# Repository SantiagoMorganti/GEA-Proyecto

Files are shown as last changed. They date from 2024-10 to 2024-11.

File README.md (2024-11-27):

<div align="center">

# PROYECTO GEA

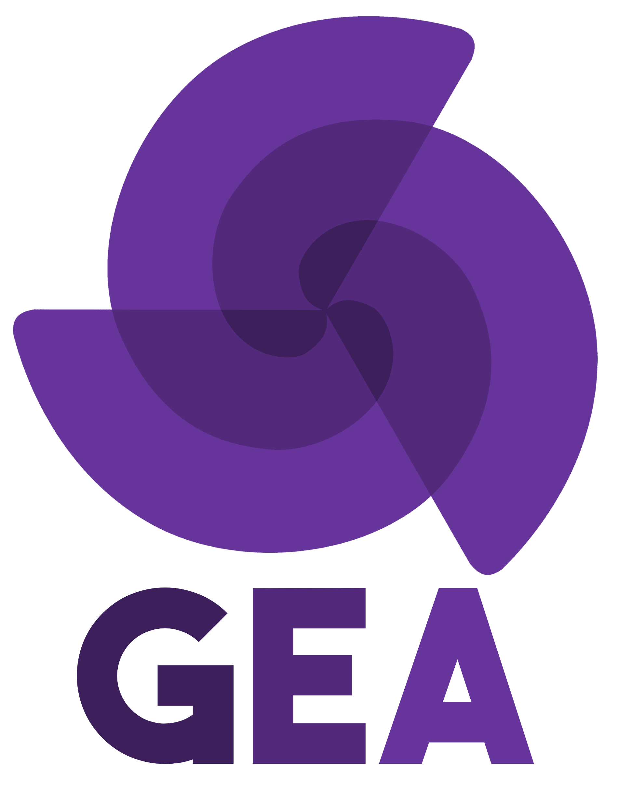
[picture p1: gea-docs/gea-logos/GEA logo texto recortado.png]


</div>

## ¿Qué es PROYECTO GEA?

PROYECTO GEA es una turbina horizontal con un modelo innovador, que busca expandir el uso de energías no contaminantes dándole un enfoque urbano a la muy desaprovechada energía eólica. Ya que es un proyecto orientado al cuidado ambiental, decidimos hacer uso de las formas empleadas por la propia naturaleza, y así nos topamos con el número dorado. Este número irracional es extraído de una serie infinita de números llamada Sucesión de Fibonacci, que cuando es graficada toma la forma de una espiral, la cual puede verse en la forma de las galaxias, en las caracolas de mar, en los huracanes, entre otras cosas. Inspirándonos en esto y avalados por múltiples estudios sobre su plausibilidad, desarrollamos un generador eólico que aprovecha con gran eficacia los lentos vientos de las ciudades para convertirlo en energía eléctrica.

## ¿Por qué decidieron hacerlo?

Esta es la manera que hallamos de ahondar en uno de las tópicos más importantes de las últimas décadas: El uso de las energías renovables. El reciente 'boom' de popularidad y el fácil acceso a los paneles solares impulsó a muchísima gente a aprovechar las energías renovables, solo para llevarse una gran decepción al ver el inalcanzable precio. La aristocratización de las energías renovables es lo que no permite que el público general pueda hacer algo para ayudar a mejorar el lugar en el que vivimos, y desde GEA estamos dispuestos a cambiar eso.

## Dónde encontrarnos

<div align="center">

| Página web | Email | Instagram |
|---|---|---|
|[Conócenos](https://gea-impatrq.web.app/)|contacto.gea.impa@gmail.com|[@proyecto.gea.24](https://www.instagram.com/proyecto.gea.24/)|

</div>

## Integrantes
 ### Dominguez Plankenhorn, Mirko Joaquin
 - mirkojdominguez@gmail.com
 ### Giampaolo, Leandro Tomas
 - leangiampaolo@gmail.com
 ### Morganti, Santiago
 - santimorganti8@gmail.com
 ### Rodriguez Vanini, Tobías Ezequiel
 - rodriguezvaninieze2@gmail.com
 ### Sipaczenko, Gregorio
 - gregorysipa@gmail.com
 ### Sosa, Gustavo Ariel
 - sosagustavoar@gmail.com

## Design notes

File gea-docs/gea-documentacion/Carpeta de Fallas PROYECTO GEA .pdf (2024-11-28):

## Carpeta de Fallos Equipo GEA

En este documento se confeccionará una lista de fallos en orden cronológico, junto con los motivos de la aparición de cada inconveniente y la posible solución que encontramos. A lo largo del año pudimos superar nuestras expectativas y acercarnos más de lo esperado a nuestra idea del proyecto final teniendo en cuenta que, además de nuestra inexperiencia, una parte de las dificultades que afrontamos en la creación del proyecto se relacionan con que el mismo consiste en replicar algo que lleva poco tiempo desde su concepción. A continuación, se detallan los fallos.

- Problemas en la selección del motor. Durante el comienzo del año pudimos contar con la oportunidad de utilizar un motor de lavarropas industrial trifásico brushless reciclado. Creíamos que tener un motor que nos podía entregar un alto voltaje por sus 3 fases era una muy buena opción, pero descubrimos lo costoso que es trabajar con un motor de esas características, provocando que a fin de año además de los rectificadores de alta potencia que armamos tengamos que añadir un transformador de 30V para reducir su voltaje (la otra opción era la utilización de un step down pero no era viable por su precio elevado). Tampoco tomamos en cuenta el torque del mismo.
Posible solución: Una posible solución de este problema sería que utilicemos otro tipo de motor, como por ejemplo uno de un ventilador de techo.
- Problema con la colocación de las poleas. Al no tener en cuenta lo dicho anteriormente colocamos la propia polea del lavarropa en la parte superior del eje, aumentando así las revoluciones del motor, perdiendo fuerza necesaria para el giro del motor. Las soluciones que encontramos a esto fueron o igualar las poleas o invertirlas, colocando la polea grande en el motor y diseñando en 3D algún tipo de ranura para que la correa se pueda acoplar.
- Problema con el tamaño de las palas. El reducido tamaño de las palas del proyecto conformaron una hélice a un 60% de su tamaño esperado, esto tuvo que ver con la cortadora láser que utilizamos y lo costoso que era utilizar una plancha entera para cada pala. La solución podría haber sido informarnos para poder reparar la cortadora láser y seguir buscando sponsors para así pagar las planchas de PAI. (https://es.wikipedia.org/wiki/Poliestireno_de_alto_impacto)
- Problema con el termoformado de las palas. El material que utilizamos (PAI) (https://es.wikipedia.org/wiki/Poliestireno_de_alto_impacto) fue la mejor opción que encontramos para realizar la hélice y aún lo sostenemos, pero el trabajo que hicimos para termo formarlas fue ineficiente lo que provocó que hubieran imperfecciones en las mismas, ya que al aplicarle calor con la pistola de calor este se dispersa de manera uniforme, generando que en algunas partes de la lámina se comience a hinchar y en otras no llegue a la temperatura suficiente para comenzar a doblarse . Las soluciones que encontramos a esto fueron: sumergir las láminas del polímero en agua caliente, así el calor sería uniforme permitiendo que toda la lámina se doble y no se hinche por el calor excesivo de la pistola de calor. La otra opción, pero mucho más costosa, hubiera sido construirla de metal mediante inyección, al no conseguir ningún sponsor relacionado a la metalistería era inviable el precio que teníamos que pagar para hacer los moldes de la hélice y para hacerla de metal aún más.
- Problema con el sistema de viraje. Si bien en un principio se trataba de un adicional, la compleción del sistema de viraje fue muy beneficiosa para el proyecto. El inconveniente con este fue que la propia hélice, al ser más pequeña, no llega a recibir la suficiente fuerza de viento de sus extremos para orientarse independientemente.
- Problema para el uso remoto de la Raspberry Pi Pico W. El último problema con el que nos topamos fue la alimentación del microcontrolador. Nuestra solución era conectarle una batería de 5V, pero las únicas de estas características son las utilizadas por los drones y su precio es alto. Al utilizarlo decidimos conectar directamente la computadora, pero para el uso que nosotros queremos darle al generador es inviable. Las soluciones más prácticas que vimos fue utilizando step down o buck converter, detalladas a continuación su solución con un diagrama de las conexiones, y los materiales necesarios para construirlas.

Primera Opción:
Usa un buck converter para reducir de 24V a 5V, con una batería que se carga y respalda la Raspberry Pi.

Componentes:
Transformador (24V).
Controlador de carga: TP4056 (para baterías de litio)
Batería recargable: Li-Ion 18650 o LiFePO4 (3.7V nominal o superior). Step-Down (Buck Converter): LM2596 configurado a 5V.
Diodo Schottky (opcional): 1N5819 (para evitar retorno de corriente).

Transformador(24V)
│
├──> Controlador de Carga ───> Batería (3.7V/12V)
│
└──> LM2596 ───> Raspberry Pi Pico W (5V)

Segunda Opción:
Usa un diodo Zener y resistencia para mantener la salida en 5V, con batería para respaldo.

Componentes:
Transformador (24V).
Controlador de carga: TP4056
Batería recargable: Li-Ion 18650 o LiFePO4 (3.7V nominal o superior). Diodo Zener: 1N4733 (5.1V, 1W).
Resistencia: 1 kΩ - 2.2 kΩ.

Transformador(24V)
│
├──> Controlador de Carga ───> Batería (3.7V/12V)
│
└──> Resistencia + Zener ───> Raspberry Pi Pico W (5V)

Tercera Opción:
Usar un divisor de voltaje, pero al consultar con profesores nos dijeron que no era lo recomendable ya que al no tener un consumo de corriente y vernos obligados a limitar la entrada a 5V, lo más probable es que se termine quemando.
- Problema con la PCB: al cambiar el conexionado a último momento, incluyendo un transformador en el circuito final, la case que teníamos no fue útil y el circuito quedó al aire libre. También durante la muestra al rotar el sistema de viraje para demostrar su funcionamiento el cable que utiliza el ACS712 se tense demasiado provocando que el ACS se suelte de la pcb. Solución de estos problemas: diseñar otra case y hacerla con un poco de tiempo y soldar de nuevo el ACS a la placa de cobre, con más tiempo a favor sería conveniente realizar la pcb nuevamente para que este perfecta.

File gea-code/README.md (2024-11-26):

# CÓDIGO DEL MICROCONTROLADOR

Implementación de un servidor de Microdot para la trasmisión inalámbrica a tiempo real de los parámetros de tensión, corriente, potencia consumida por la carga y frecuencia de giro de la salida del generador.

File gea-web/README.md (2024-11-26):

Directorio para los archivos relacionados con la página web del PROYECTO GEA

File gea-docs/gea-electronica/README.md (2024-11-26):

Directorio para las fotografías y documentación electrónica del proyecto.

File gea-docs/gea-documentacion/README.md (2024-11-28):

Directorio para todos los documentos informativos realizados a lo largo del año.

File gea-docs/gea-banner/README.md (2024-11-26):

Directorio para el banner del proyecto, a ser expuesto en la 32° muestra anual de proyectos.

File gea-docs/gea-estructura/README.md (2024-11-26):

Directorio para las imágenes de la estructura del proyecto y todo su desarrollo.

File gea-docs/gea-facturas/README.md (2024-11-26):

Directorio para las facturas de compra realizadas hasta el dia de la fecha.

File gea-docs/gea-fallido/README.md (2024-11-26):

Directorio para demostrar que a veces fallamos.

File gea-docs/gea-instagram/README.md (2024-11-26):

Directorio para todos los archivos relacionados con la cuenta de Instagram de PROYECTO GEA.

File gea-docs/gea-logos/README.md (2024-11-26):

Directorio para todos los archivos multimedia del PROYECTO GEA. Incluye logos, texto, etc.

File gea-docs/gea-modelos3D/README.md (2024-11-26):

Directorio para todos los archivos en el tópico de impresion 3D, modelado y animación.

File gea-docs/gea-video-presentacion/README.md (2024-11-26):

Directorio para el video presentación del PROYECTO GEA.

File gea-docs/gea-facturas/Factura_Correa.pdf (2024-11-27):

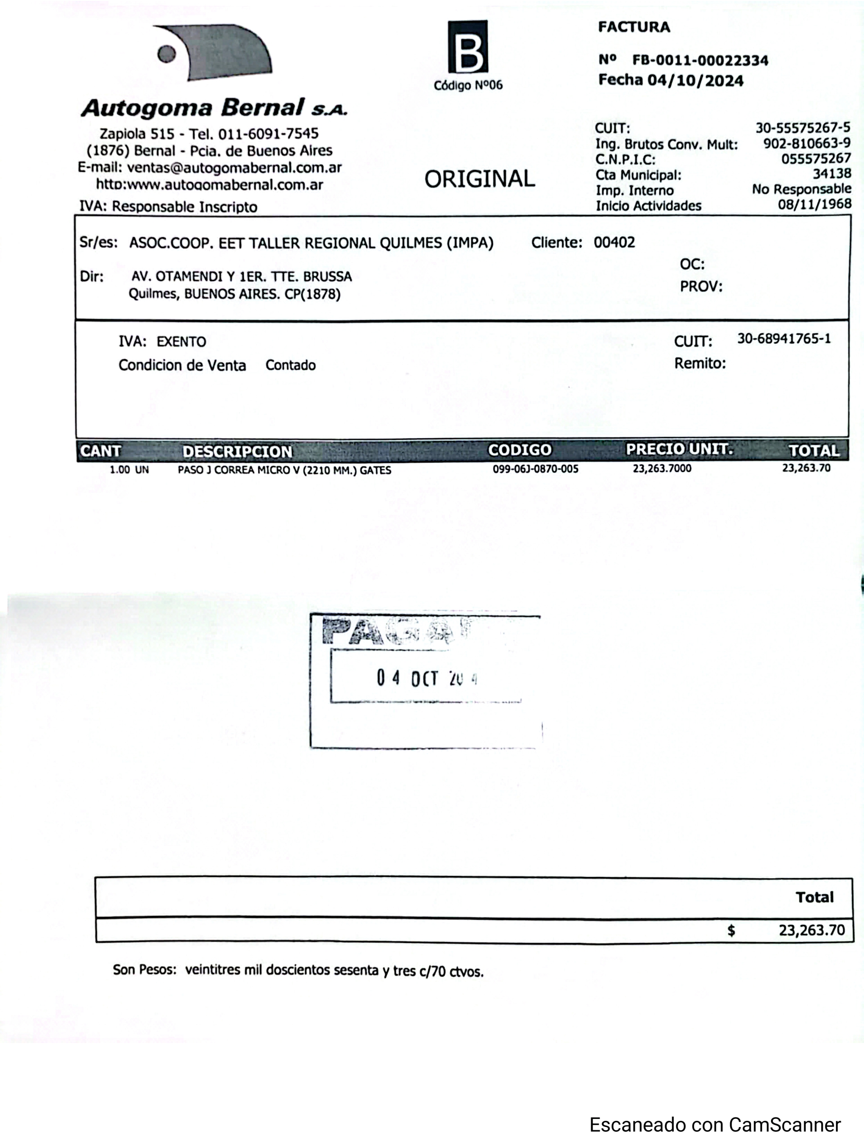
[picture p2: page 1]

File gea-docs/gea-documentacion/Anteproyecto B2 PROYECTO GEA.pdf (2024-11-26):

Escuela de Educación Técnica Nº7
Taller Regional Quilmes
Prácticas Profesionalizantes: Especialidad Aviónica

# Generador Eólico

## Presentación de anteproyecto

## Título del proyecto:

No sé qué poner. Falta nombre del proyecto en sí y un logo

## Integrantes:

- DOMINGUEZ PLANKENHORN, Mirko Joaquín (mirkodominguezplankenhorn@impatrq.com)
- GIAMPAOLO, Leandro Tomás (leandrotomasgiampaolo@impatrq.com)
- MORGANTI, Santiago
(santiagomorganti@impatrq.com)
- RODRIGUEZ VANINI, Tobías (tobiasrodriguezvanini@impatrq.com)
- SIPACZENKO, Gregorio
(gregoriosipaczenko@impatrq.com)
- SOSA, Gustavo Ariel
(gustavoarielsosa@impatrq.com)

## Objetivo del proyecto:

El objetivo del proyecto es sacar provecho del uso de la energía eólica en zonas con un gran consumo energético, fomentando así el uso de energías renovables. Para esto se construirá una turbina de viento de gran eficiencia de forma que, por ejemplo, se pueda aprovechar el gran potencial eólico en las zonas del sur del país. Otro ejemplo de uso sería el de las zonas urbanas donde se utiliza principalmente la energía solar, las represas hidroeléctricas que alimentan gran parte del país, o en veleros por su tamaño reducido.

## Utilidades del proyecto:

En la Argentina, la energía eólica representa solo un 8% del total de energía producida, ya que los altos costos de transporte y la economía inestable no permiten el crecimiento del sector. Es conveniente expandirse en este territorio e invertir en estas energías renovables debido al alto potencial eólico que tiene nuestro país (sobre todo en el territorio de Tierra del Fuego, Chubut, Río Negro y otras zonas del sur argentino) y hoy en día no existe una propuesta a nivel nacional para solventar los problemas de rentabilidad de la producción de este tipo de energía, entonces lo que buscamos con este proyecto es poder hacer rentable la producción de turbinas de viento para diversos usos, haciendo uso de la impresión 3D y el reciclaje de baterías.

## Descripción del funcionamiento:

Proponemos un diseño compacto de una turbina de viento, pensado para ser de fácil elaboración, transporte e instalación en diversos contextos, sea urbano y de uso personal o de producción en masa.

El proyecto consta de un generador de energía eólica con una hélice diseñada en forma de espiral que utiliza el principio de la espiral de Fibonacci, para así aprovechar más el viento captado por la misma y trabajar con una menor velocidad del viento. Posee un sistema de viraje para direccionar y corregirse de manera autónoma con la dirección del viento, así aumentando la eficacia y la producción energética.

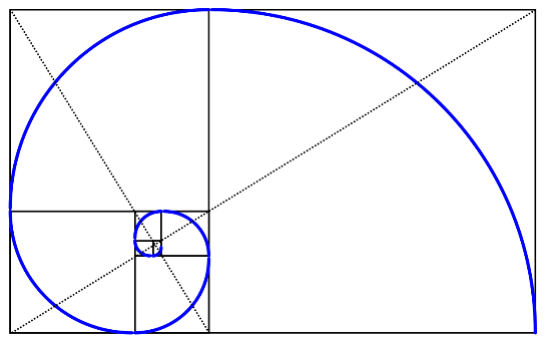
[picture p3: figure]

La energía cinética que produce el movimiento de la hélice por acción del viento pasa hacia un motor brushless trifásico, transformándola en energía mecánica y pasando por un multiplicador, elevando su rpm y desencadenando en un generador convirtiendo la energía mecánica en eléctrica. Esta energía entonces sería almacenada en baterías, recicladas de dispositivos electrónicos y ubicadas debajo del sistema de viraje.

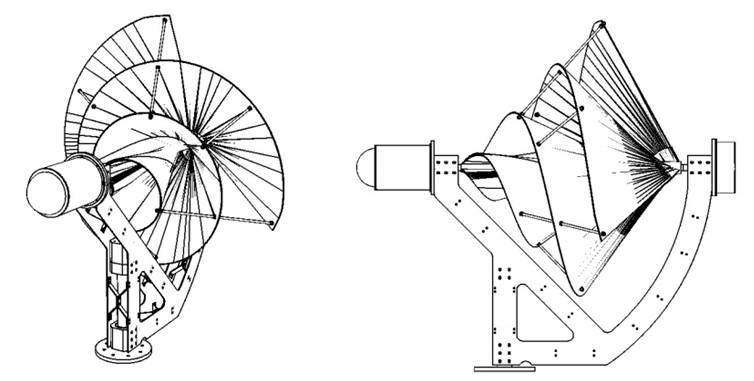
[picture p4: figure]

## Análisis de factibilidad:

- Diseño de la hélice:
- Diseño en 3D de la figura inicial de la hélice en FreeCad.
- Simular el diseño en SOLIDWORKS para así poder verificar su aerodinámica
- Una vez impreso el diseño, hacer una prueba en la vida real del proyecto en el túnel de viento presente en la escuela.

- Conversión de energía cinética en eléctrica:
- Necesitamos de un motor para realizar la conversión de energía cinética en eléctrica, para esto reciclamos un motor de lavarropa y lo reutilizamos en el proyecto.
- Necesitamos un multiplicador para poder así aumentar el número de vueltas de la hélice en bajas velocidades del viento. Para esto utilizaremos la polea del propio motor que ya poseemos.
- Rectificar la corriente para trabajar de manera nominal, para esto disponemos de conocimientos sobre rectificación.
- Estructura:
- Diseñar una estructura de base estable en la que se sostenga la hélice y presentarla.
- Diseñar los carriles inferiores que permitan la introducción del sistema de viraje de la hélice.
- Almacenamiento de energía:
- Hacer uso de baterías recicladas de dispositivos electrónicos, por ejemplo, de notebooks/computadoras portátiles. No disponemos de los conocimientos exactos acerca de estas baterías.
- Diseño y armado del sistema de almacenamiento de energía.

## Costo del proyecto:

- Filamento para impresora 3D: Gratis
- Motor trifásico brushless: Gratis (Utilizamos un motor reciclado)
- Polea tambor del motor: $16.000
- Correa motor: $6.000
- Circuito rectificador de onda completa: $3.000
- 4 diodos de potencia
- 1 capacitor
- 1 bobina
- 1 placa de cobre
- Materiales para la estructura: Serán utilizados materiales que tenemos en nuestras casas, y poseemos las herramientas suficientes para poder trabajarlas.
- Cable: Utilizaremos los cables que estén a nuestra disposición en el establecimiento si es que coinciden con la potencia requerida, usaremos los que tenemos en nuestras casas o compraremos.
- Baterías: Reciclaremos las baterías de dispositivos electrónicos.

Estimamos un costo total de más de $25.000.

## Análisis de costo/beneficio:

*** inicio contenido reemplazable ***

En base al desarrollo de costos hecho arriba, analizar que las magnitudes de medios económicos a emplear sean acordes a los disponibles ya sea por Cooperadora o por aportes propios.

Una buena herramienta para la confección de este análisis es ver como ahora mismo se está resolviendo el problema, y comparar las utilidades conseguidas si se aplica la solución tecnológica que proponen. También se puede comprar a nivel costos como cada utilidad (más allá del beneficio directo) repercute a nivel costo en el entorno en donde se desea plantear la solución.

En definitiva, no solo deberían intentar justificar por que razón se financiaría su proyecto (más allá del costo que involucra) sino por qué alguien estaría interesado en replicarlo (y usarlo), teniendo en cuenta los costos detrás (de desarrollo y manteniemiento por ejemplo).

*** fin contenido reemplazable ***

## Diagrama en bloques del prototipo:

El proyecto (nombre) se desarrolla de la siguiente manera:

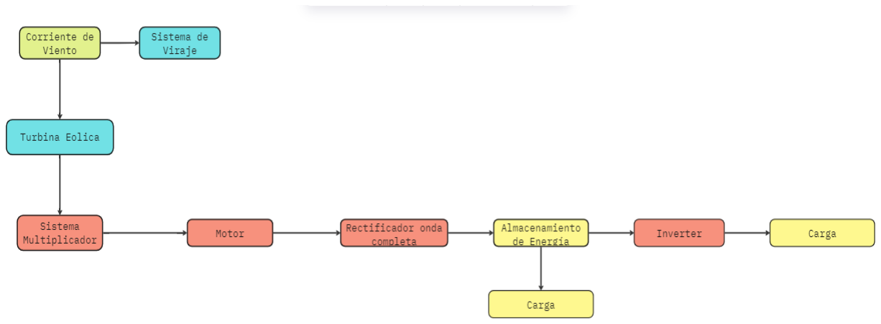
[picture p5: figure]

## Diagrama de tiempo de desarrollo:

*** inicio contenido reemplazable ***

Debe mostrar el avance del proyecto en el tiempo entre el periodo del 08 de Marzo al 20 de Noviembre del corriente año.

Es un diagrama que muestra la cantidad de tiempo que se va a dedicar a cada tarea. Se deben poner metas realistas para hacer en un tiempo realista, es decir, no poner metas muy grandes, teniendo poco tiempo para hacerlas, ni tampoco dedicar mucho tiempo a metas sencillas. Nosotros visualizamos esta gestión de tareas gracias a un diagrama de gantt.

Es una herramienta gráfica cuyo objetivo es exponer el tiempo de dedicación previsto para diferentes tareas o actividades a lo largo de un tiempo total determinado.

Ejemplo:

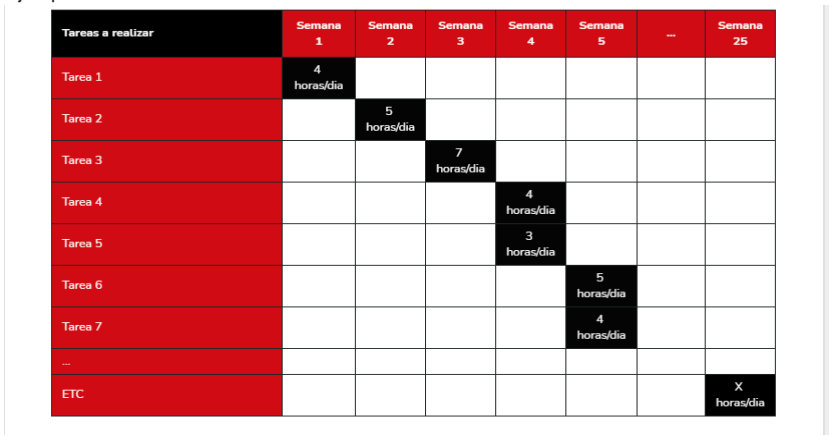
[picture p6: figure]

El diagrama de arriba fue desarrollado usando Venngage. (https://es.venngage.com/templates/charts/gantt) Tiene muchas plantillas para que puedas hacer tu propio diagrama de gantt, personalizandolo como a vos te guste, además que se puede hacer directamente en la página.

Les recomendamos usar Miro para aprovechar la misma herramienta de diseño. Dejamos un link para un template de Gantt:
https://miro.com/templates/gantt-chart/

*** fin contenido reemplazable ***

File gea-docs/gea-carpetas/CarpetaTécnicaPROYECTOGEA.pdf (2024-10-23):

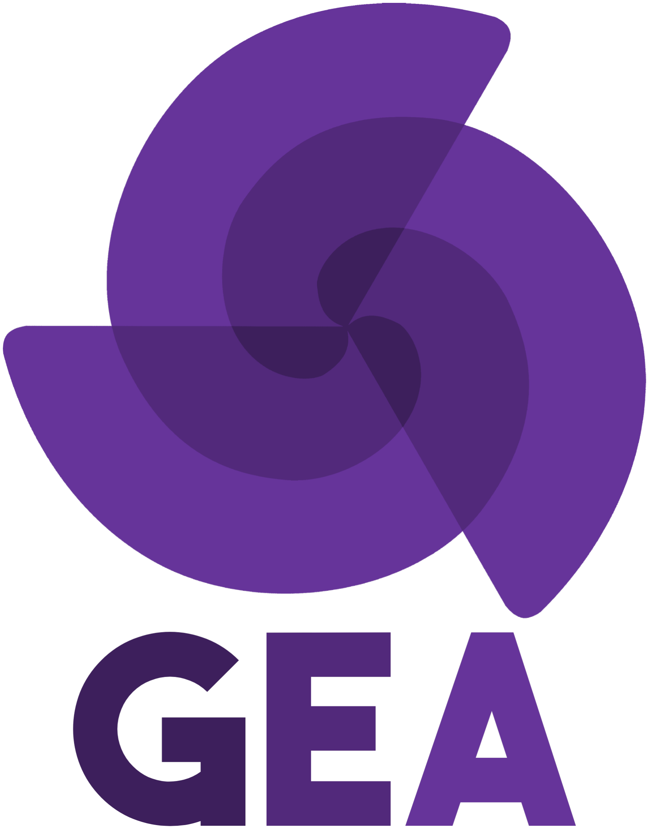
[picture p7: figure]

# Carpeta Técnica

# PROYECTO GEA

# 7mo 1ra Comisión B Año 2024

## Dominguez Plankenhorn, Mirko Joaquin Giampaolo, Leandro Tomas Morganti, Santiago Rodriguez Vanini, Tobias Ezequiel Sipaczenko, Gregorio Sosa, Gustavo Ariel

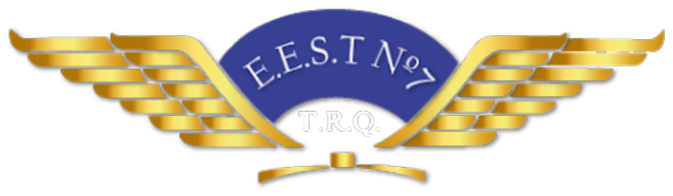
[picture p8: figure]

´

# Indice general

1 Exordio | 2
2 Introduccion | 6
3 Fundamentos | 8
4 Estructura y composición | 11

# Capítulo 1

# Exordio

## 1.1. Integrantes

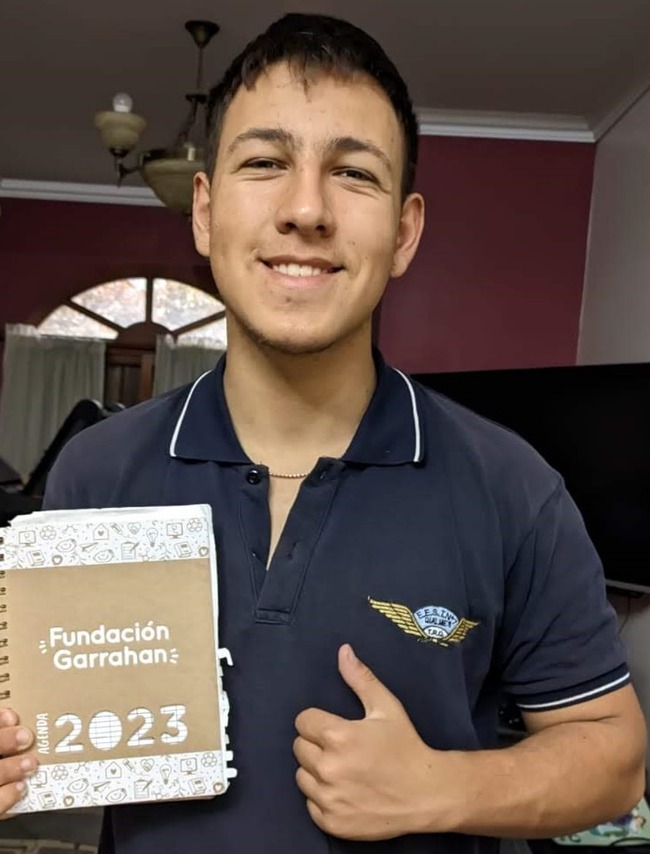
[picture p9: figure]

Mirko Joaquin Dominguez Plankenhorn

DNI: 47119776

Mail: mirkojdominguez@gmail.com

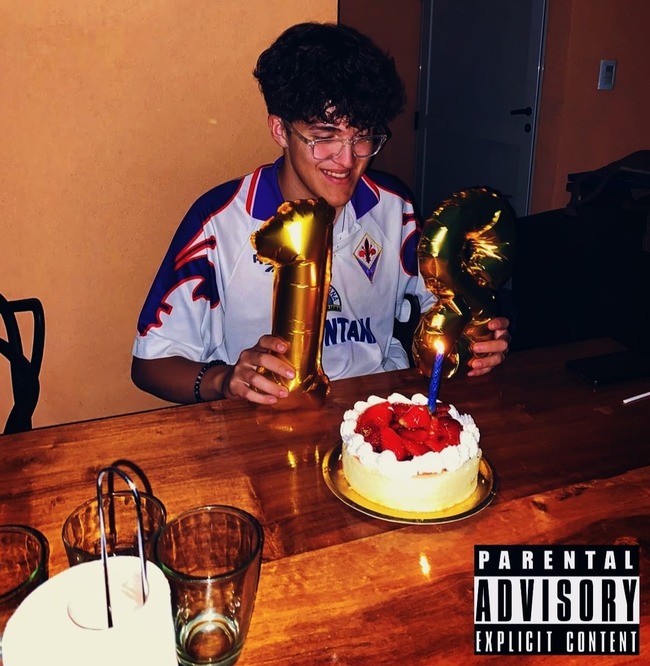
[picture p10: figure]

Leandro Tomas GiampaolO

DNI: 46909172

Mail: leangiampaolo@gmail.com

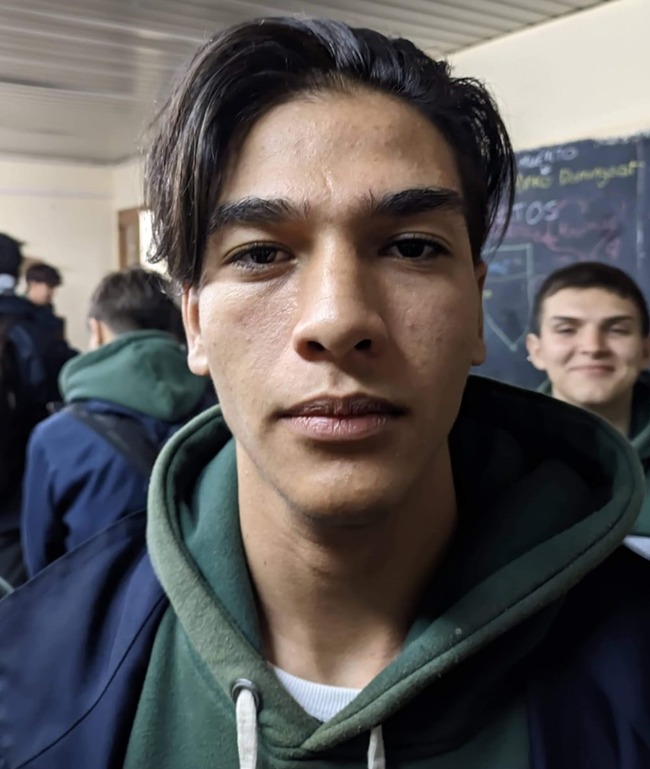
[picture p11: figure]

Santiago Morganti

DNI: 46822132

Mail: santimorganti8@gmail.com

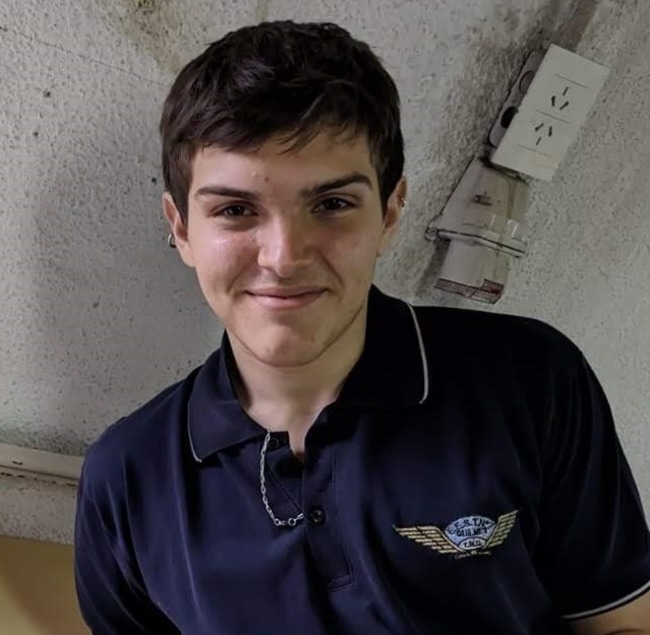
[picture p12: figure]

Tobias Ezequiel Rodriguez Vanini

DNI:

Mail: rodriguezvaninieze2@gmail.com

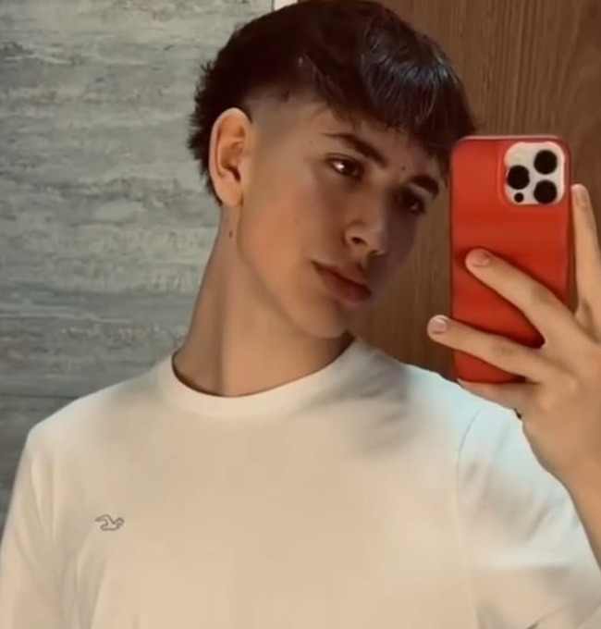
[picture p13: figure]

Gregorio Sipaczenko

DNI:

Mail: gregorysipa@gmail.com

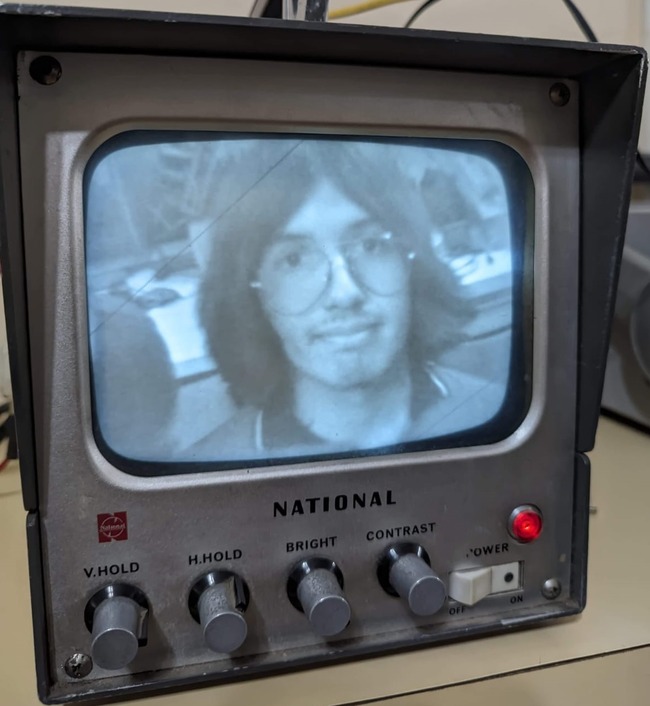
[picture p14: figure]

Gustavo Ariel Sosa

DNI: 46898131

Mail: sosagustavoar@gmail.com

# Image

Figura 1.1: Los miembros del equipo GEA.

## 1.2. Medios de contacto

Mail de contacto: @contacto.gea.impa@gmail.com Cuenta de Instagram: @proyecto.gea.24 (https://www.instagram.com/proyecto.gea.24/)
Página Web: Web Oficial del PROYECTO GEA (https://steamuserimages-a.akamaihd.net/ugc/914666421766753316/D1A52816907A945F5B7B2B1F0E9A4CB2C42F9CEA/) Repositorio Oficial de GitHub: Gea-Proyecto (https://github.com/SantiagoMorganti/GEA-Proyecto)

## 1.3. Agradecimientos

A los profesores a cargo de nuestras horas de trabajo:

Carlassara, Fabrizio.

Medina, Sergio.

Bianco, Carlos.

Argüello, Gabriel.

Palmieri, Diego.

A los profesores que colaboraron en torno al progreso del proyecto:

Lima, Gabriel.

Solomiewicz, Nicolas.

Claramunt, Diego.

Scicolone, Julian Patricio.°°°

A la Asociación Cooperadora del IMPA;
A la Fuerza Aérea Argentina por la donación de una batería;
A todos aquellos medios de difusión ya sea radial, virtual o cualquier otro medio, por el apoyo brindado al proyecto; Al personal docente y no docente de la institución por su vital colaboración.

# Capítulo 2

# Introduccion

## 2.1. ¿Qué es PROYECTO GEA?

PROYECTO GEA consiste en una turbina eólica áltamente eficiente cuyo comportamiento responde a la forma de sus tres aspas, las cuales conforman una espiral. Asimismo, la turbina cuenta con una aplicación diseñada para el seguimiento de sus parámetros de funcionamiento.
Se conoce genéricamente como turbina a una turbomáquina que se ve atravesada por un fluído, el cual inscribe una fuerza tangencial sobre su rotor (generalmente acompañado de aspas), provocando el movimiento de su eje para la posterior conversión de la energía cinética resultante en la energía que se desee.
En lo que respecta a la aplicación de seguimiento de sus parámetros, se trata de un programa de Microdot escrito mayoritariamente en lenguaje C, JavaScript, CSS, entre otros, que se encarga de obtener y mostrar los datos que el usuario pueda necesitar, como la velocidad de giro, la tensión entregada, etcétera.

## 2.2. Impacto esperado

### 2.2.1. Impacto local

Argentina posee algunas de las condiciones climáticas más favorables de Latinoamérica en lo que se refiere al aprovecha-miento de los vientos, ya que cuenta con dos de las cinco ciudades más ventosas del mundo: Rio Gallegos y Ushuaia. A pesar de que estas ciudades son sin lugar a dudas las más idóneas para la utilización del generador, en provincias como Buenos Aires o La Pampa, los vientos a lo largo del año promedian entre los 21 y los 28 km/h, una velocidad más que suficiente para que prolifere nuestro generador.

### 2.2.2. Impacto continental y mundial

PROYECTO GEA es la primer turbina con forma de espiral áurea del continente americano, una de las primeras en el mundo en ser llevada a cabo, y tiene capacidad de sobra para convertirse en un estandarte de la utilización de la energía eólica de manera accesible en los ambientes urbanos.
La expansión del uso de las energías renovables es crucial para trabajar en conjunto hacia el objetivo planteado en el Acuerdo de Paris contra el Cambio Climático firmado por 195 paises en abril de 2016: Reducir el aumento de temperatura global a un número por debajo de los 1.5°. Lejos de bajar, este número continua en alza desde 2019. Bajo nuestro punto de vista, proyectos como este que faciliten y abaraten el acceso y ayuden a inculcar el uso de energías limpias son cruciales para el progreso en torno a la causa previamente mencionada. En paises como Estados Unidos, Brasil o México, que se encuentran en el puesto 2, 7 y 10 respectivamente como los paises con más emisiones de CO2 en el mundo, es vital que se continue impulsando el uso de enegías renovables.

## 2.3. Ventajas

El simple hecho de que PROYECTO GEA pueda ser considerado un pionero en la re-imaginación de la energía eólica para los ambientes urbanos hace que la relación entre las ventajas y desventajas que conlleva aplicar el producto sea aplastante. Para enumerar algunas de ellas podemos nombrar:

Un notable beneficio económico para el consumidor gracias a la reducción de costes, a la generación de ahorro y a la evitación de las elevadas tarifas de los proveedores de energía, sujetas a la variación del precio de los combustibles fósiles.

Un inmejorable aporte a la crítica situación que respecta al frenado del calentamiento global, eliminando por completo la emisión de gases de efecto invernadero.

Mejora la calidad del aire y del agua que consumimos y respiramos, reduciendo así sustancialmente las enferme-dades provocadas por la contaminación.

Descentraliza el mercado de las energías renovables, planteando una novedosa y eficaz alternativa contra las costosas aplicaciones de paneles solares.

## 2.4. Estado del Arte

Actualmente, la única empresa en el mundo que está desarrollando una turbina con la proporción áurea lleva el nombre de Liam F1 Archimedes. (https://thearchimedes.com) A pesar de que su nombre pueda apuntar a que se trata de una espiral de Arquímedes y no una espiral dorada, su nombre se debe en realidad a un guiño al Tornillo de Arquímedes, (https://es.wikipedia.org/wiki/Tornillo_de_Arquímedes) que tiene una forma similar.

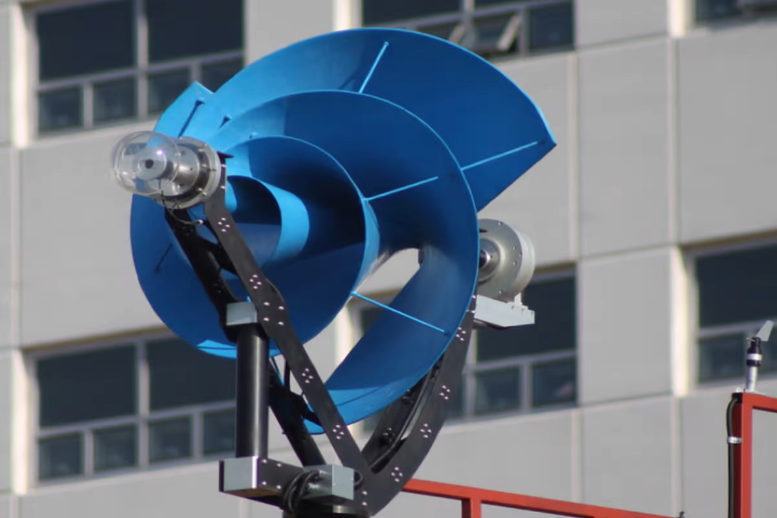
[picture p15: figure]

Figura 2.1: Una turbina Liam F1 Archimedes.

# Capítulo 3

# Fundamentos

## 3.1. Conceptos previos

El punto focal de funcionamiento de una turbina es la conversión de energía cinética a mecánica. En nuestro caso empleamos la energía eólica, y la forma en la que la máquina logra convertir dicha energía es a traves del movimiento de una serie de aspas, palas o cuchillas conectadas a un rotor, a las cuales se le imprime una fuerza tangencial producto del empuje del viento.
Esta fuerza tangencial hace que el rotor gire, habilitándolo a aprovecharse de una de las tantas formas del Principio de Conservación de la Energía, en forma de dos leyes: la Ley de Lenz y la Ley de Faraday.
Antes de hincar en la explicación de dichas leyes, es necesario contar con una serie de conocimientos previos, detallados a continuación.

### 3.1.1. Lagrangiano

Un Lagrangiano es una función escalar confeccionada para representar una gran cantidad de importantes propiedades de un sistema dinámico, como su evolución en el tiempo; se trata de la forma más cómoda y completa de realizar este análisis. Lo que se suele hacer es, para un sistema concreto, establecer coordenadas generalizadas y normalizar los parámetros estudiados, afín de observar el comportamiento del sistema bajo estas condiciones, y para ser más específico, las variaciones visibles. En caso de que no haya variaciones en alguno de los parámetros al aplicarse las condiciones normalizadas, se ha hallado una simetría contínua. En lo que compete al tema tratado en este documento, lo que se busca es exactamente eso: hallar simetrías, lo cual indica que se cumple el Teorema de Noether.

### 3.1.2. Teorema de Noether

El Teorema de Noether expresa que en un sistema físico, cualquier simetría que pueda hallarse se corresponde con la constancia de una magnitud de dicho sistema, es decir, se corresponde con alguna de las leyes de conservación. Se llega a esta conjetura relacionando dos pilares de la física: la independencia de la forma de una ley física de cualquier transformación que preserve el sistema de coordenadas, y la otra es la ley de conservación de una magnitud física.
En este caso específico, al aplicar el Teorema de Noether al lagrangiano del sistema, se podrá hallar que el mismo es independiente al valor del tiempo, indicando que existe conservación de la energía. Dicha asunción nace del siguiente desarrollo.
Partiendo desde el siguiente Lagrangiano invariable temporalmente:

L = (qi
, q˙i

, t) = (qi

, q˙i) | (3.1)

siendo

L = Lagrangiano

qi = Coordenadas generalizadas al i-ésimo grado de libertad del sistema.

q˙i = Velocidades generalizadas al i-ésimo grado de libertad del sistema

i = Grados de libertad del sistema (es decir, puede tomar un valor entre 1 e i grados de libertad)

De este lagrangiano se obtiene:

∂L
∂t = 0 | (3.2)

Ya que existe una constancia, es decir, una invariancia con respecto a un parámetro del sistema, cuando se aplica el Teorema de Noether se puede determinar que existe energía conservada. Dicha energía se expresa como:

E =

X

i

q˙i

∂L
∂q˙i
− L | (3.3)

donde E es la cantidad de energía conservada, y recibe el nombre de Energía de Lagrange.
Posteriormente, se deriva E con respecto al tiempo y se aplica un mecanismo para simplificar el sistema y evaluar la evolución del lagrangiano en el tiempo, llamado Ecuaciones de Euler-Lagrange. Asi, obtengo:

dE
dt
= 0 | (3.4)

De esta forma, se entiende que si la variación a lo largo del tiempo (determinada por la derivación) es igual a cero, la Energía de Lagrange es constante en el tiempo, lo que se traduce en la Ley de Conservación de la Energía.

### 3.1.3. Ley de Conservación de la Energía

Cuando hablamos de mecánica clásica, uno de sus pilares es la Ley de Conservación de la Energía. La misma dicta que, en un sistema aislado, la energía no se crea ni se destruye, sino que solo se transforma.
Es sobre este mismo principio que se amparan las energías renovables hoy disponibles en el mundo; se trata de artilugios que aprovechan las fuerzas generadas por un tipo de energía disponible eternamente para humanidad y la convierten en otro, generalmente siendo este otro la energía eléctrica.
El método de conversión de energía mecánica a eléctrica comúnmente utilizado en sistemas como turbinas, consta del uso de dos leyes que nacen del Principio de Conservación de la Energía: la Ley de Lenz y la Ley de Faraday.

### 3.1.4. Fuerza electromotriz

En materia de electromagnetismo, se conoce con el incorrecto nombre de Fuerza electromotriz (fem) al fenómeno de inducción eléctrica producido por una fuente no eléctrica medido en voltios. Si bien dicho fenómeno puede ser producto de la aplicación de fuerzas físicas sobre una carga eléctrica, el nombre de ”Fuerza.es una reliquia histórica ocasionada porque ese fue el nombre que Alessandro Volta, su creador, le otorgó al momento de descubrirla. La razón por la que se dice que el fenómeno ”puede”ser producto de fuerzas físicas es porque la Ley de Faraday, explicada más adelante, dice que la fem nace del movimiento de líneas de campo, por lo tanto, puede aparecer tanto en casos en los que a través de fuerzas físicas se mueva el inductor que genera el campo como en casos en los que el inductor no se mueva pero su campo sea variable.

### 3.1.5. Flujo magnético

Se conoce con el nombre de Flujo magnético y la letra ϕ, a la medida de cantidad de magnetismo, es decir, la interacción magnética (tanto negativa como positiva) en un punto del espacio que es atravesado por un campo. Afín de visualizarlo, puede decirse que el flujo magnético es proporcional a la cantidad neta de líneas de campo que atraviesen en cualquier sentido, sumándose y restándose aquellas con dirección opuesta. Los componentes que constituyen el valor de ϕ son la cantidad de líneas de campo que atraviesan un punto, la superficie sobre la cual actuan dichas líneas y el ángulo de incidencia de estas líneas de campo en el punto contemplado.

## 3.2. Ley de Faraday

La Ley de Faraday es una ecuación que describe que el valor de fem en un circuito cerrado es directamente proporcional al cambio a lo largo del tiempo del flujo magnético.
Otro nombre que recibe la Ley de Faraday es Ley de Faraday-Lenz, puesto que ambas leyes van muy de la mano a la hora de explicar el funcionamiento de los generadores eléctricos. Lo que dicta la Ley de Lenz es que la polaridad de la fem en un conductor a causa de la variación de flujo magnético en el tiempo producirá una corriente y por consecuencia un campo magético, el cual se opondrá siempre a las variaciones de la corriente que lo generó. Teniendo estas dos leyes en cuenta, podemos establecer las siguientes fórmulas:

Para describir el valor de flujo de campo magnético en movimiento:

ϕ =

Z

−→S

−→B · d

−→S | (3.5)

siendo

ϕ = Flujo magnético, medido en W b(weber)

−→S = Superficie definida por el conductor.

−→B = Inducción magnética, medida en T(tesla)

Por lo tanto, según las leyes descrita en este apartado, la tensión inducida ε será igual a:

ε = −N

dϕ
dt

(3.6)

donde el signo negativo (−) en la fórmula será la representación de la oposición al cambio de ϕ establecida en la Ley de Lenz, N será la cantidad de espiras del conductor y dϕ
dt

la variación de flujo magnético en el tiempo.

Una vez asentados los conceptos previos, se torna una tarea simple comprender los principios que dan lugar a nuestro proyecto. La producción de energía de una turbina eólica es en su totalidad debida al Principio de Conservación de la Energía; cuando una corriente de viento la atraviesa, una serie de aspas conectadas a un rotor comienzan a girar a causa de la fuerza tangencial impresa por la resistencia aerodinámica. Al final de dicho rotor hallamos una serie de bobinas, que con su giro inducen en las bobinas de otro componente, el estator, una corriente por Ley de Faraday. Finalmente, la corriente eléctrica generada es transmitida hacia una batería, cargándola.

# Capítulo 4

# Estructura y composición

## 4.1. Hélice

Para poder determinar y finalmente concretar la idea principal del proyecto que decidiéramos llevar a cabo a lo largo del año, el inicio cualquier tipo de desarrollo fue precedido por una intensa investigación, la cual nos llevó a dar con el concepto perfecto. Además de nuestra fascinación con las energías sostenibles, hallamos (y probamos) modelos de turbinas increíblemente novedosos que no estaban siendo desarrollados en nuestro lado del mundo, por lo que nuestros primeros encuentros con las llamadas Turbinas de Fibonacci representaban una modernidad que estábamos totalmente dispuestos a adoptar. A lo largo de todo nuestro desempeño escolar, dada la elección que tomamos a la hora de continuar con el camino de la educación secundaria, nos vimos rodeados de aeronaves con turbinas convencionales, y aprendimos tanto sus principios de funcionamiento como algunas novedades que se podrían implementar para amplificar su rendimiento. De esta forma, dimos con las turbinas espirales y posteriormente con las que siguen la espiral dorada.

### 4.1.1. El número áureo

El número áureo, comúnmente representado por la letra griega φ, es un concepto matemático que comprende múltiples áreas de las cosas como las conocemos, como pueden ser la arquitectura, el arte o la naturaleza. El número áureo, también llamado razón dorada, se define como la proporción donde la relación entre la suma dos cantidades a y b y la cantidad mayor a, es igual a la relación entre la cantidad mayor y la cantidad menor. Esto se define matemáticamente como:

φ =

a + b
a

=

a
b

(4.1)

Para poder entenderlo mejor, la misma razón puede expresarse de múltiples maneras, por ejemplo, partiendo desde:

φ = 1 +

1
φ

(4.2)

que indica que, partiendo de un segmento en el que se toma una sección mayor = φ y una sección mayor = 1, la relación entre el segmento completo = φ + 1 y la parte menor es igual a la proporción entre el segmento mayor y el segmento menor. Por lo tanto, puede determinarse mediante fracciones contínuas que:

φ = 1 +

1
φ

−→ φ = 1 +

1
1 + | 1
1+ | 1
1+ | 1
1+...

(4.3)

incrementando la exactitud cuantas más fracciones se hagan, demostrando así la irracionalidad del número φ.

### 4.1.2. El rectángulo áureo

Como lo dicta su nombre, un rectángulo dorado es aquel que posee una proporcionalidad entre sus lados igual a la razón áurea. Otro nombre con el que se lo conoce es Rectángulo de Euclides, puesto que fue éste quien lo obtuvo y fue capaz de demostrarlo.

h

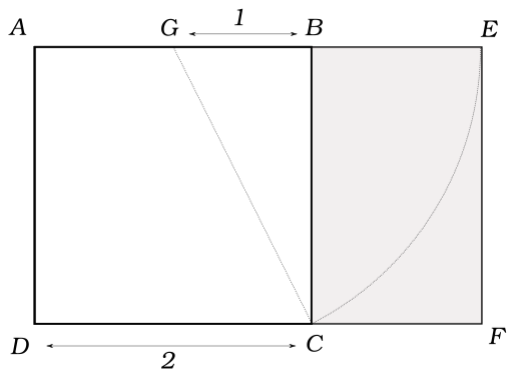
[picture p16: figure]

Figura 4.1: El Rectángulo de Euclides.

Demostración del Rectángulo de Euclides

En la Figura 4.1 pueden apreciarse tres formas:

El rectángulo principal, de vértices AEF D, lado mayor AE y lado menor AD, considerado áureo ya que la razón entre su lado mayor y menor es igual al número φ;

El cuadrado interior, de vértices ABCD, cuyos lados son iguales y tienen un valor de dos unidades;

El triángulo rectángulo, de vértices GBC cuyo vértice G supone la mitad de la sección AB del cuadrado, de lados GC (hipotenusa), GB (Cateto adyacente al ángulo de referencia) y BC (Cateto opuesto al ángulo, igual al lado del cuadrado)

Para comenzar, se observa que puede calcularse la longitud de la hipotenusa, aplicando el Teorema de Pitágoras:

GC² = GB² + BC² = 1² + 2² = 5 | (4.4)

por lo tanto se entiende que GC =

√
5 | (4.5)

A continuación, se prolonga el segmento GC hasta intersectar la recta AE en el punto E, obteniendo que, puesto que G es el centro del círculo que pasa por B, C y E, se puede deducir que:

GE = GC =

√
5 | (4.6)

Así, siguiendo la proporción áurea: AE = AG + GE = 1 + √
5 | (4.7)

de donde, finalmente:
AE
AD =

1 + √
5
2
= φ | (4.8)

que verifica la proporción áurea.

Una propiedad notable de este rectángulo es que, además del rectángulo principal de vértices AEF D, también existe el rectángulo de vértices BEF C, que también cumple con la razón dorada. Si se aplica el mismo procedimiento aplicado sobre el rectángulo principal al segundo rectángulo, se verá que se forma un tercer rectángulo de proporciones doradas así como el primero dio lugar al segundo. Si se traza una recta desde los vértices opuestos del rectángulo principal y una desde los vértices opuestos del segundo rectángulo, puede verse que son perperndiculares y se cruzan en un mismo punto: este es el punto de convergencia de la espiral dorada.

### 4.1.3. La espiral dorada

La Espiral dorada es una espiral logarítmica originada a partir de una serie de rectángulos dorados. En la ecuación (4.3), se observa una convergencia hacia φ, que es a su vez una de las formas más acertadas de representar el número áureo; cualquier intento de representación con números enteros dará lugar a, en el mejor de los casos, aproximaciones inexactas. Lo que le da forma a esta espiral es una ecuación polar idéntica a las que dan forma a una espiral logarítmica común, pero con el grado de crecimiento b = ln φ
La ecuación que describe la espiral es:

r(θ) = aφ˙

θ
(4.9)

siendo

r = Distancia desde el origen en coordenadas polares;

θ = Angulo en radianes; ´

a = Constante que controla el tamaño de la espiral;

φ = En este caso representa la razón de crecimiento y el sentido de la espiral.

Si bien esta es la ecuación que la describe, la manera en la que se construye la espiral es mucho más simple. Como se ha demostrado, al momento de trazar la recta que divide al rectángulo en sus dos secciones cuya proporción es igual a φ, puede verse que debajo de la sección mayor obtengo un cuadrado y debajo de la sección menor obtengo otro rectángulo que cumple con la proporción de oro.

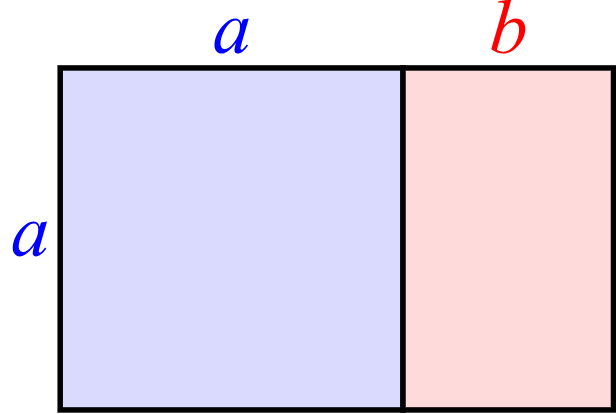
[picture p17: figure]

Figura 4.2: El cuadrado está coloreado en azul y el rectángulo secundario, en rojo.

Visto que el rectángulo secundario b, el rectángulo terciario que se formará cuando éste se divida, y así infinitamente, pueden ser divididos de la misma manera ya que cumplen con la proporción áurea, puedo unir con una circunferencia los vértices opuestos de los infinitos cuadrados debajo de las secciones mayores de cada rectángulo para dar lugar a la siguiente espiral:

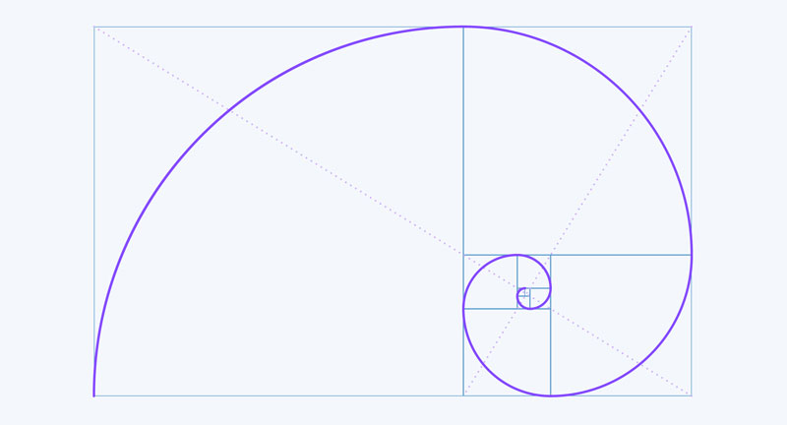
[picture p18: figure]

Figura 4.3: La espiral dorada.

### 4.1.4. La sucesión de Fibonacci

Como ya se ha hecho alusión previamente, los números enteros son una cuando menos inexacta iteración de la razón áurea. Uno de estos ejemplos es la Sucesión de Fibonacci, una serie infinita de números naturales compuesta por dos números, los cuales dependiendo de la referencia acostumbran a ser 0 y 1 o 1 y 1, y a partir de estos, cada termino siguiente es igual a la suma de los dos anteriores. Por ejemplo, los primeros veinte términos son:

0, 1, 1, 2, 3, 5, 8, 13, 21, 34, 55, 89, 144, 233, 377, 610, 987, 1597, 2584, 4181... | (4.10)

La particularidad de esta serie es que, por ejemplo, al construir bloques cuya longitud de lado sea igual a los valores de la serie, se forma una aproximación al rectángulo áureo.

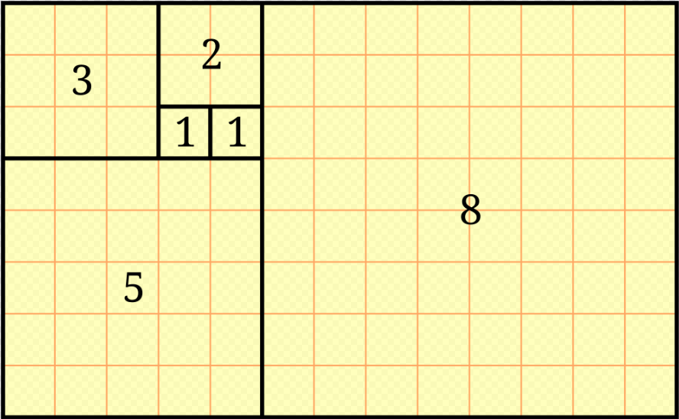
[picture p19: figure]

Figura 4.4: Una aproximación al rectángulo áureo, usando los dígitos 1, 1, 2, 3, 5 y 8 de la sucesión de Fibonacci.

Asimismo, si se traza una circunferencia entre los vértices opuestos de los cuadrados que corresponde a cada uno de los términos de la serie, se obtiene una aproximación a la espiral áurea.

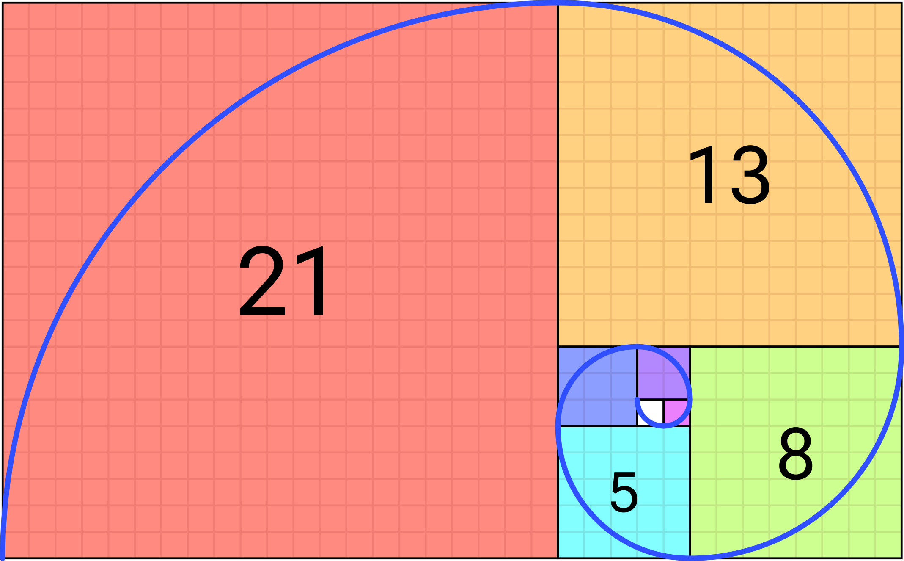
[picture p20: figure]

Figura 4.5: La aproximación a la espiral áurea, utilizando los dígitos 1, 1, 2, 3, 5, 8, 13 y 21.

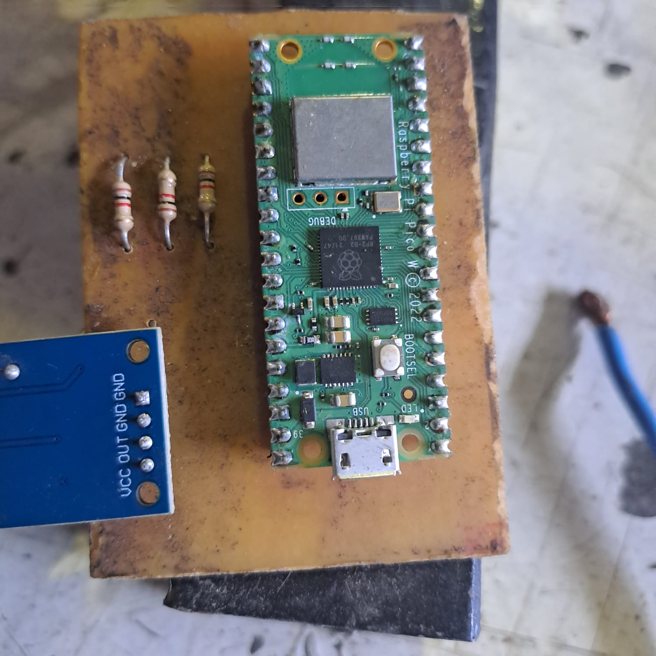
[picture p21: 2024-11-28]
gea-docs/gea-electronica/PCB final.jpg

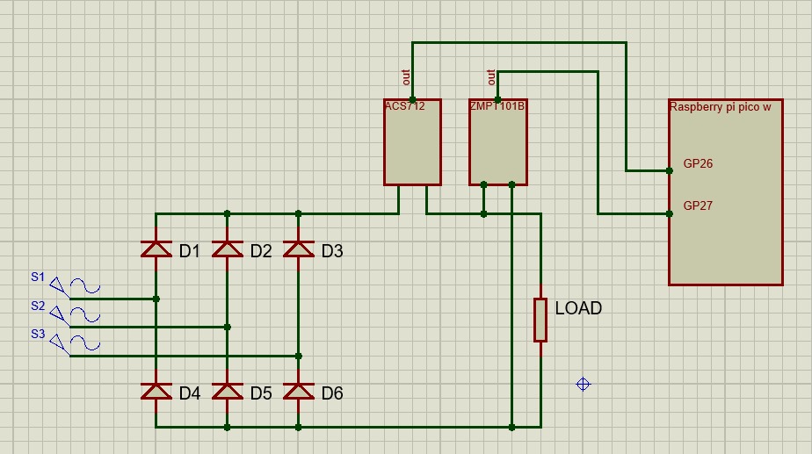
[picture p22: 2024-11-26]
gea-docs/gea-electronica/Esquemático Monitoreo GEA.jpeg

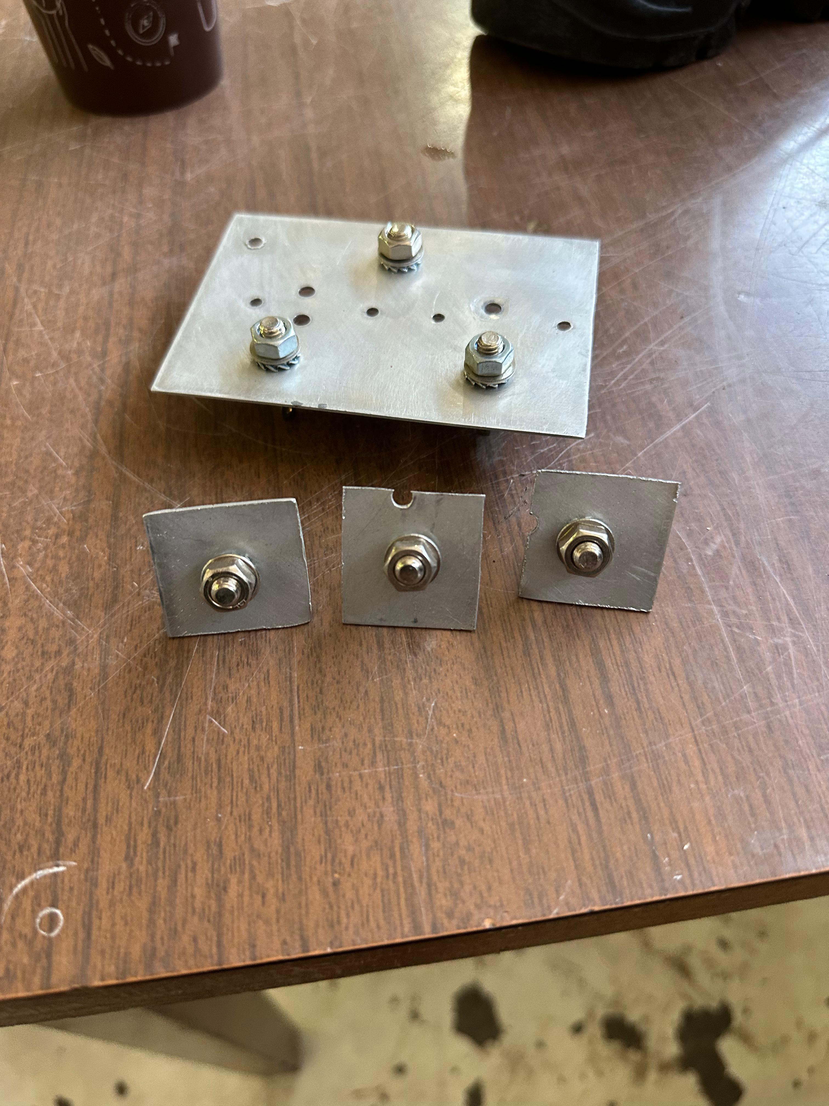
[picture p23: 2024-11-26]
gea-docs/gea-electronica/Diodos montados en disipador de calor.jpeg

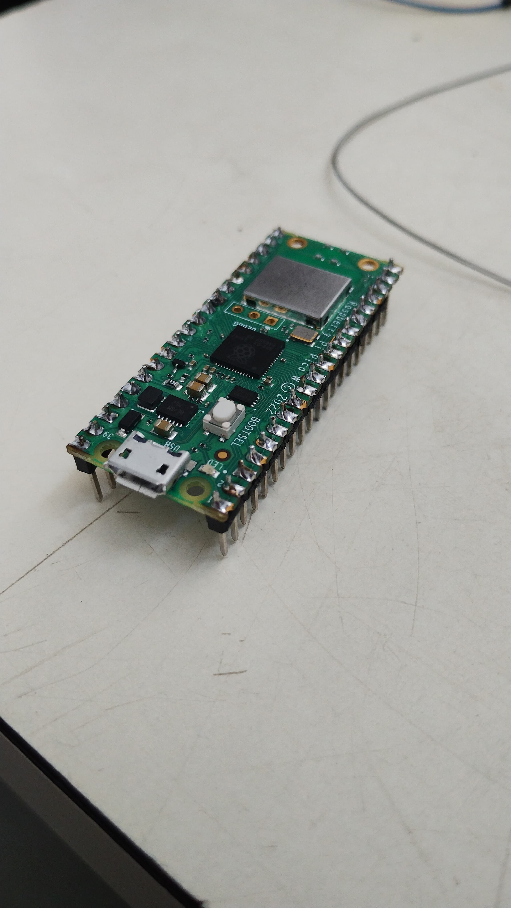
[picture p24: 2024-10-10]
gea-docs/gea-electronica/soldadura cabezales gpio.jpeg

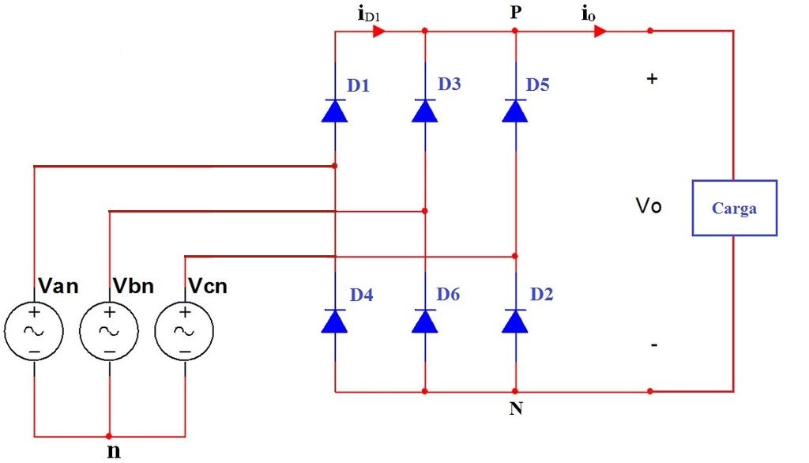
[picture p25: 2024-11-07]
gea-docs/gea-electronica/Circuito rectificador trifasico.jpeg

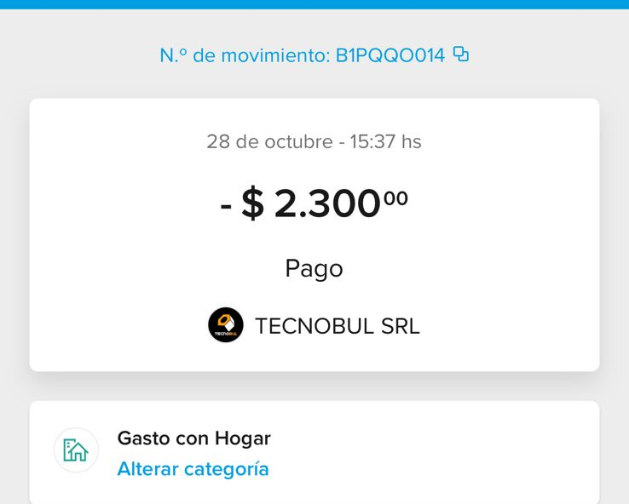
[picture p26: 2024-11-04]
gea-docs/gea-facturas/Comprobante_De_Pago_Ferreteria.png

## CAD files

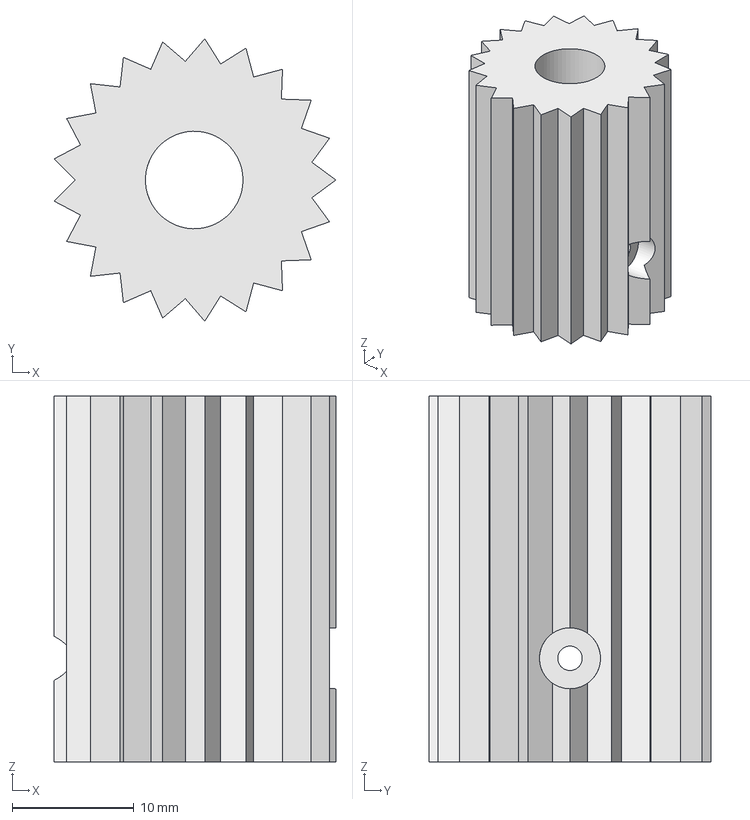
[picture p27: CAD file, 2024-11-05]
gea-docs/gea-modelos3D/AgarrePolea.FCStd
23.1 x 23.2 x 30.0 mm

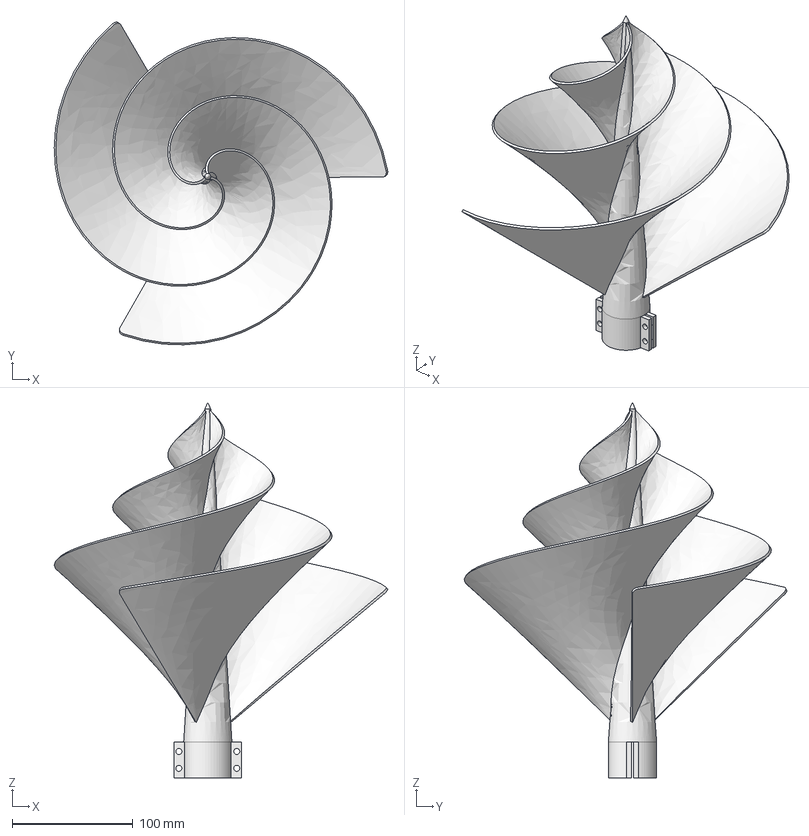
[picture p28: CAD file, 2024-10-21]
gea-docs/gea-modelos3D/PROTOTIPO A ESCALA.FCStd
276.5 x 267.5 x 310.9 mm

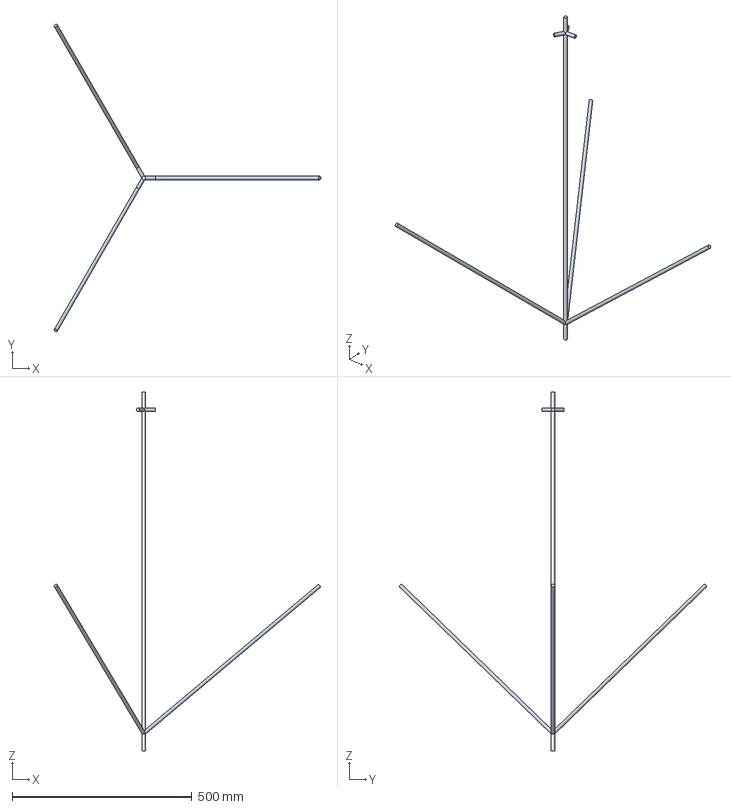
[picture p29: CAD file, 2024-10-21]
gea-docs/gea-modelos3D/HELICE.FCStd
743.2 x 856.7 x 1000.0 mm

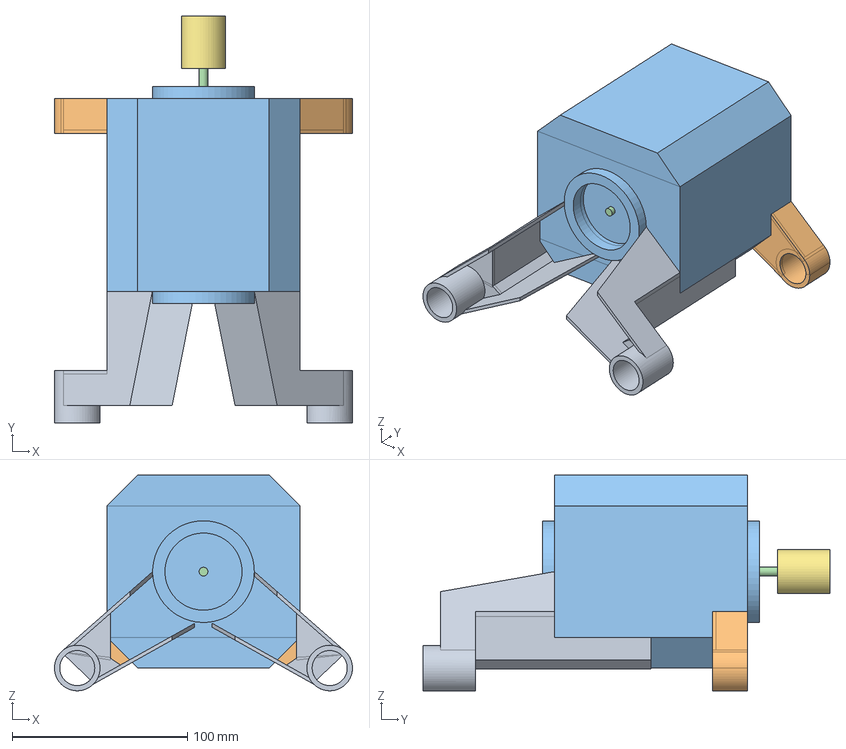
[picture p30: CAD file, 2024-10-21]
gea-docs/gea-modelos3D/MOTOR.FCStd
170.0 x 232.0 x 123.0 mm

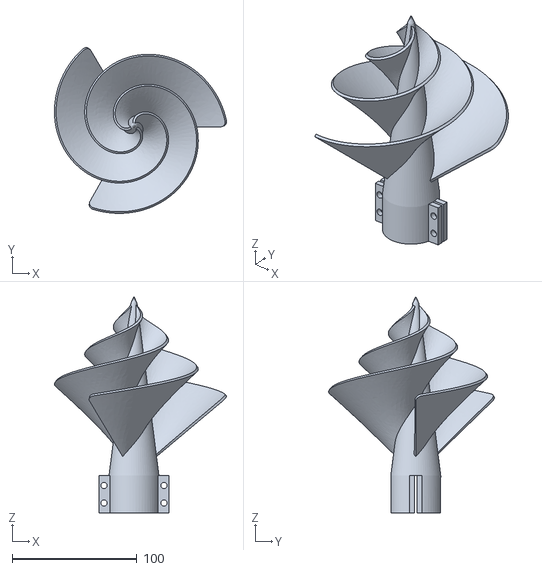
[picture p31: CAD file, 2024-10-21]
gea-docs/gea-modelos3D/PrototipoHeliceEscala.stl
137.8 x 132.7 x 172.9

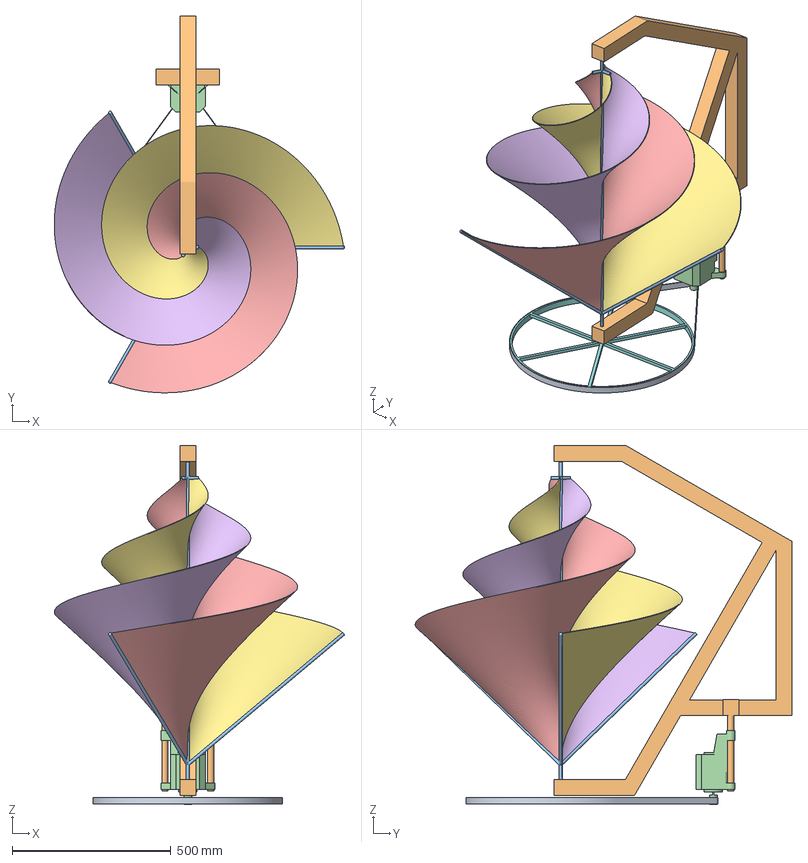
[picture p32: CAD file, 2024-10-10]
gea-docs/gea-modelos3D/modelo GEA.FCStd
913.5 x 1184.4 x 1129.0 mm
motor (Meshed)
estructura (Meshed)
ALAMBRES (Meshed)
Fusion014 (Meshed)
aleta3 (Meshed)
aleta2 (Meshed)
aleta 1 (Meshed)
Polea (Meshed)
Correa (Meshed)

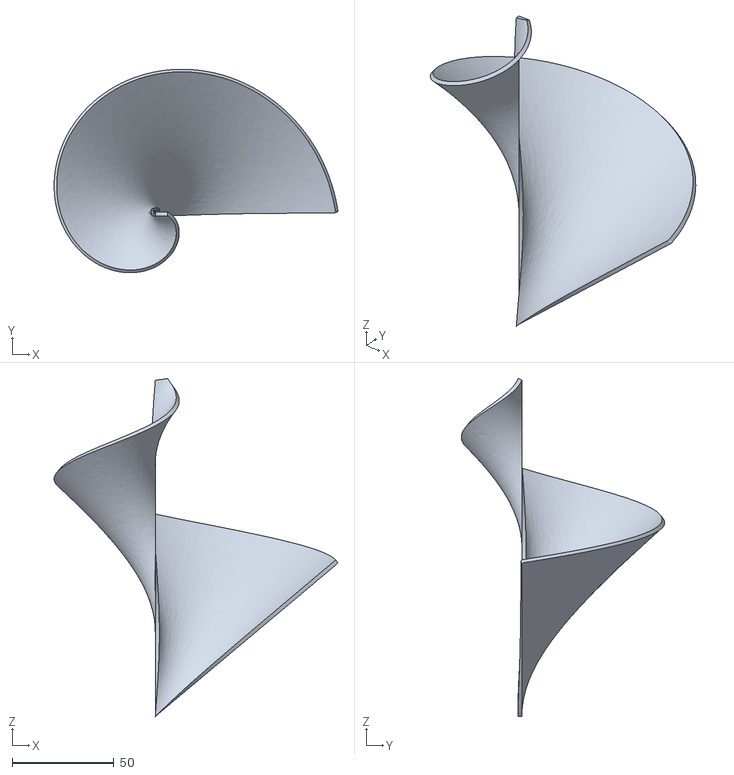
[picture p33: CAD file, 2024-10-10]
gea-docs/gea-modelos3D/PrototipoAletaImpresion.stl
139.6 x 100.1 x 166.3

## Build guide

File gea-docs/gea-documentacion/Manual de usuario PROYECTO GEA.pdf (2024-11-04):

# Manual de usuario del proyeto G.E.A

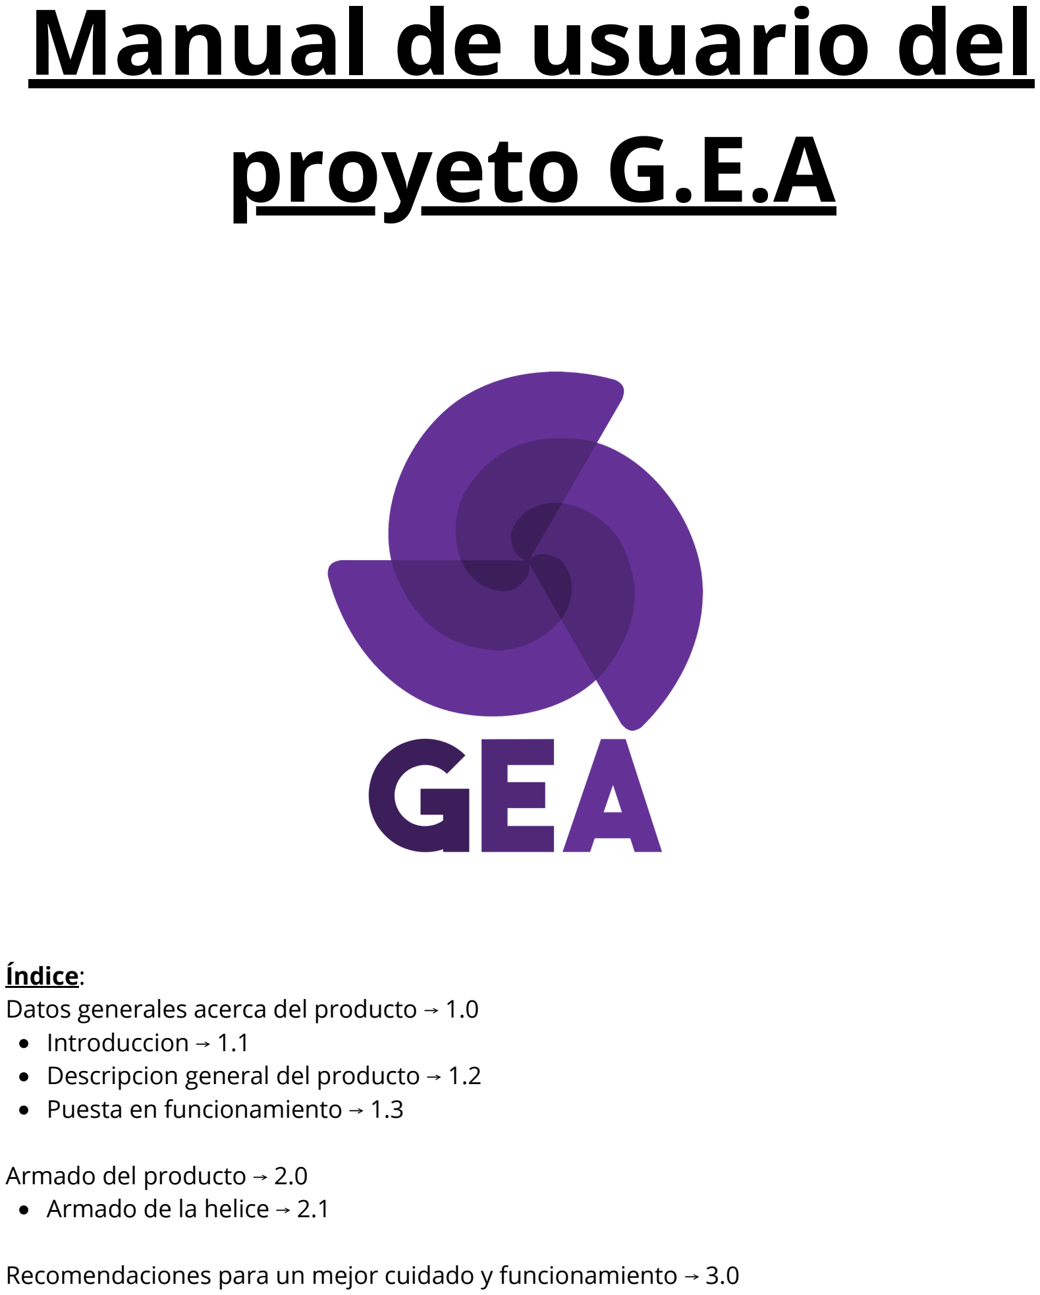
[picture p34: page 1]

Índice:
Datos generales acerca del producto ⟶ 1.0 Introduccion ⟶ 1.1
Descripcion general del producto ⟶ 1.2 Puesta en funcionamiento ⟶ 1.3

Armado del producto ⟶ 2.0
Armado de la helice ⟶ 2.1

Recomendaciones para un mejor cuidado y funcionamiento ⟶ 3.0

1.0

# Datos generales acerca del producto

1.1

## Intoducción

En el mundo de las energias renovables, la energia solar es el principal metodo de generacion de energia. En G.E.A nos dimos cuenta de que a la energia eolica es un metodo muy efectivo y que con un cambio de diseño en la estuctura se podia exprimir mucho mas su potencial. Con este nuevo diseño pudimos implementar el uso de la energia eolica en zonas urbanas, brindado una opcion mas efectiva y comoda a la energia solar.
1.2

## Partes del producto

G.E.A es un producto que consta de 6 partes: La helice
El eje
El motor
La correa de goma
La estructura
El circuito de monitoreo inalambirco
1.3

## Puesta en funcionamiento

Para poner el producto en funcionamiento, por favor seguir los siguientes pasos: Situar el generador en una zona elevada, donde se encuentre la mayor circulacion de viento y haya la menor obstaculizacion al mismo.

1.

2.Orientar la helice del generador a la direccion de donde viene el viento.
3.Conectar las baterias al rectificador.
4.Encender el ciruito de monitoreo inalambrico

2.0

# Armado del producto

En esta sección del manual le explicaremos paso a paso la forma correcta de armar el Generador Eolico.

## Paso 1

Primeramente hay montar el eje en la base, para esto hay que pasar el eje por el centro de los rulemanes.

## Paso 2

Luego de pasar el eje por el centro de los rulemanes, lo que hay que hacer es arrmar la helice. Para esto usted encontrara tres paletas con forma espiralada, las paletas tienen un orden especifico para poder ser ensambladas, por lo que marcamos cada una para que pueda identificarlas.

## Paso 3

Encastrar la rueda con el eje, en el lado posterior de la helice.

## Paso 4

Poner la correa de goma, la misma tiene que enganchar a la rueda y a la rosca del motor. La correa tiene que quedar en tension para que no patine ni se salga por los costados.

## Paso 5

Para poder poner la correa en tension, se tiene que desajustar las tuercas que se encuentran en la parte interior de la estructura. Luego mueva el soporte del motor hasta el punto en el que la correa quede con la tension necesaria y por ultimo vuelva a ajustar las tuercas.

3.0

# Recomendaciones para un mejor funcionamiento y cuidado

A continuacion, le damos algunas recomendaciones para que pueda darle un mejor cuidado y funcionamiento a su Generador Eólico.

Corroborar que la correa tenga la tension nescesaria para evitar la fatiga de la misma y no perder energia cinetica

Al menos una vez a la semana verificar que la correa se encuantre en buen estado

Lo ideal seria pintar la estructura con pintura anticorrosiva cada 3 a 5 años, en el caso de que se encuentre en zonas de alta humedad y lluvias, recomendamos que lo haga al menos una vez al año.

De ser posible, recomendamos que ponga el generador bajo un techo para evitar cualquier tipo de desgaste que se pueda generar debido a el clima.

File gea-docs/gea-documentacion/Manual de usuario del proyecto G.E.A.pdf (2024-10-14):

# Manual de usuario del proyecto G.E.A

Índice:

Datos generales acerca del producto ⟶ 1.0

Armado del producto ⟶ 2.0

Armado de la helice ⟶ 2.1

Introduccion ⟶ 1.1
Descripcion general del producto ⟶ 1.2 Funcionamiento ⟶ 1.3

1.0

# Datos generales acerca del producto

1.1

## Intoducción

En el mundo de las energias renovables, la energia solar es el principal metodo de generacion de energia. En G.E.A nos dimos cuenta de que a la energia eolica es un metodo muy efectivo y que con un cambio de diseño en la estuctura se podia exprimir mucho mas su potencial. Con este nuevo diseño pudimos implementar el uso de la energia eolica en zonas urbanas, brindado una opcion mas efectiva y comoda a la energia solar.
1.2

## Descripción general del producto

G.E.A es un producto que consta de 4 partes:

1.3

## Funcionamiento

Para poner el producto en funcionamiento, por favor seguir los siguientes pasos:

La helice
La estructura
Las baterias
El circuito de monitoreo inalambirco
1. Situar el generador en una zona elevada, donde se encuentre la mayor circulacion de viento y haya la menor obstaculizacion al mismo.
2. Orientar la helice del generador a la direccion de donde viene el viento.
3. Conectar las baterias al rectificador.
4. Encender el ciruito de monitoreo inalambrico

2.0

# Armado del producto

En esta sección le explicaremos como se debe realizar el armado del generdor eólico.
2.1

## Armado de la helice

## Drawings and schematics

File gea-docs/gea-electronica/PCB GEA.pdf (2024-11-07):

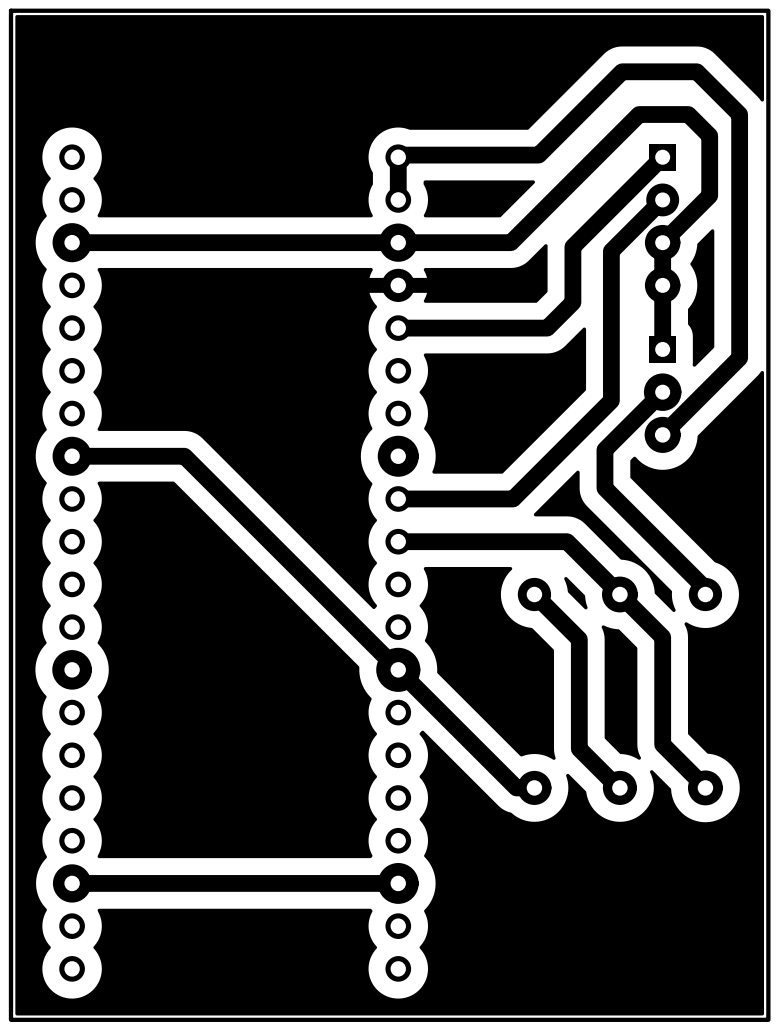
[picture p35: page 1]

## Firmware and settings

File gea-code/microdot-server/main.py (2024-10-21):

from machine import ADC, Pin
from time import sleep, ticks_us, ticks_diff
from microdot import Microdot, send_file

app = Microdot()

# Inicializar los canales ADC
adc0 = ADC(Pin(26))  # ADC canal 0 (GPIO 26) - ACS712 con divisor de tensión
adc1 = ADC(Pin(27))  # ADC canal 1 (GPIO 27) - salida del seguidor de tensión ZMP101B

# Parámetros del seguidor de tensión
offset = 1.64  # Voltaje de offset en la salida del seguidor de tensión
vp_output = 0.5  # Voltaje pico máximo (500 mVp)
adc_min_voltage = 1.14  # Voltaje mínimo esperado (correspondiente a -500mVp)
adc_max_voltage = 2.14  # Voltaje máximo esperado (correspondiente a +500mVp)
adc_resolution = 65535  # Resolución del ADC de 16 bits

# Variables para calcular frecuencia
last_cross_time = ticks_us()  # Último tiempo de cruce por cero
frequency = 0  # Frecuencia de la señal
rpm = 0  # Revoluciones por minuto

def map_adc_to_voltage(adc_value, v_min, v_max):
    """Mapear valor ADC al rango de voltaje entre v_min y v_max."""
    return adc_value * (v_max - v_min) / adc_resolution + v_min

def calculate_rms_voltage(v_peak, v_peak_max=0.5, v_rms_max=220):
    """Convertir el valor de voltaje pico a voltaje eficaz."""
    return (v_peak / v_peak_max) * v_rms_max

def calculate_rpm():
    """Detectar cruce por cero y calcular la frecuencia y RPM."""
    global last_cross_time, frequency, rpm
    
    # Leer el valor del ADC y convertirlo a voltaje
    adc1_value = adc1.read_u16()
    tension_adc1 = map_adc_to_voltage(adc1_value, adc_min_voltage, adc_max_voltage)
    
    # Detectar el cruce por cero: cuando la señal cambia de positivo a negativo o viceversa
    if tension_adc1 - offset < 0.01 and tension_adc1 - offset > -0.01:  # Cerca del cruce por cero
        current_time = ticks_us()  # Obtener el tiempo actual
        period_us = ticks_diff(current_time, last_cross_time)  # Calcular el periodo en microsegundos
        if period_us > 0:
            frequency = 1_000_000 / (2 * period_us)  # Frecuencia en Hz (2 cruces por ciclo)
            rpm = frequency * 60  # Convertir a revoluciones por minuto (RPM)
        last_cross_time = current_time  # Actualizar el último cruce por cero

def calculate_current(adc_value):
    """Convertir la lectura del ADC en corriente (A) usando el ACS712."""
    # Convertir el valor ADC a voltaje
    voltage_adc0 = map_adc_to_voltage(adc_value, 0, 3.3)
    
    # Ajustar por el divisor de tensión (multiplicar por 3/2)
    real_voltage = voltage_adc0 * 3 / 2
    
    # Convertir voltaje a corriente (según la relación del ACS712)
    current = (real_voltage - 2.5) * 30 / 2  # 2.5V corresponde a 0A, ±30A dentro de 2V
    return current

@app.route('/data')
def data(request):
    # Medir corriente desde el ACS712 en el canal 0 (GPIO 26)
    adc0_value = adc0.read_u16()
    corriente = calculate_current(adc0_value)
    
    # Medir tensión eficaz en el canal 1 (seguidor de tensión ZMP101B)
    adc1_value = adc1.read_u16()
    tension_adc1 = map_adc_to_voltage(adc1_value, adc_min_voltage, adc_max_voltage)
    tension_eficaz = calculate_rms_voltage(tension_adc1 - offset)
    
    # Calcular la frecuencia y RPM
    calculate_rpm()
    
    # Calcular la potencia
    potencia = tension_eficaz * corriente
    
    # Devolver los datos en formato JSON
    return {
        'tension_eficaz': f'{tension_eficaz:.2f}',
        'rpm': f'{rpm:.2f}',
        'corriente': f'{corriente:.2f}',
        'potencia': f'{potencia:.2f}'
    }

# Para servir el archivo estático HTML
@app.route('/')
def index(request):
    return send_file('index.html')

# Para servir los archivos estáticos (CSS, JS)
@app.route('/<dir>/<file>')
def static_files(request, dir, file):
    return send_file("/" + dir + "/" + file)

# Iniciar el servidor
app.run(debug=True, port=80)

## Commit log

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2024-10-08 feat: agregar pestaña de facturas al github del proyect.
2024-10-08 chore: Agregar carpeta y su README.md respectivo para alojar el código del microcontrolador
2024-10-08 feat:a gregar factura de compra del sensor de tension.
2024-10-08 feat: agregar factura de los diodos de potencia.
2024-10-08 Feat: Agregar el archivo de index.html para el servidor de microdot
2024-10-08 Feat: Agregar archivo de boot.py para el server de microdot
2024-10-08 Feat: Agregar archivo de main.py y código de el resto de los archivos añadidos
2024-10-08 Feat: Agregar el archivo base.js en el fichero scripts para el server de microdot
2024-10-08 Feat: Agregar archivo base.css en el fichero styles para el servidor de microdot
2024-10-08 Feat: Agregar inicialización de el ADC encargado del seguidor de tencion
    El ADC es inicializado con su resolución enfocada en la zona de operación del seguidor de tención ZMP101B
2024-10-08 Feat: Actualizar medición de tensión eficaz en index.html
2024-10-08 Feat: Medición y actualización de frecuencia de la señal o RPM en index.html
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2024-10-09 docs: añado video y foto de medicion de tension
2024-10-10 feat: arreglo de carpetas
2024-10-10 fix: corrijo la escritura del logo y agrego información adicional
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2024-10-10 fix: corrijo dimensiones del logo, agrego cuadro de Socials
2024-10-10 feat: modelo 3D en freeCAD de GEA
    [BASE Con motor.FCStd]
2024-10-10 feat: agregar animacion de blender .MP4
    [BASE Con motor.FCStd]
2024-10-10 update: nombre de archivos
    [modelo GEA.FCStd]
2024-10-10 Feat: Agregar mesh del prototipo de aleta de la hélice impresa en 3D
    [PrototipoAletaImpresion.stl]
2024-10-10 Feat: Agregar ptototipo de hélice a escala para imprimir en 3D
    [PrototipoHeliceEscala.stl]
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2024-10-16 feat: creo carpeta en docs y añado draft de la carpeta técnica
2024-10-16 Feat: Agregar diseño de la pcb del microcontrolador
2024-10-16 Feat: Implementar código de medición de salida del ACS712 con divisor de tensión en el ADC
2024-10-16 Feat: Agregar dato a tiempo real de la corriente medida a tiempo real en el server de microdot
2024-10-16 Feat: Agregar cálculo de la potencia entregada por el generador
2024-10-16 Feat: Agregar representación a tiempo real de la potencia entregada por el generador
2024-10-21 Feat: Agregar modelo 3D de solo la hélice con el sistema de agarre
    [HELICE.FCStd]
2024-10-21 Feat: Agregar modelo 3D a detalle del motor usado de generador
    [MOTOR.FCStd]
2024-10-21 Feat: Agregar capas a recortar en laser para el método de termoformado de las paletas de la hélice
2024-10-21 Feat: Agregar modelo 3D del prototipo a escala para imprimir
    [PROTOTIPO A ESCALA.FCStd]
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2024-10-22 Fix: Modificar PCB con un cambio en el divisor de tensión y espejar la imagen
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2024-10-22 Update: corte de caños para nuevo soporte de motor (el anterior no soportaba)
2024-10-22 Update: perforaciones en el nuevo soporte para el motor
2024-10-22 update: actualizo la carpeta técnica a su última versión
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2024-10-28 feat: resultado del nuevo caño para el soporte del motor.
2024-10-28 fix: correción de errores finales
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2024-10-28 Update: corte de planchas para el rulemán del eje
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2024-10-29 feat: agregar comprobante de pago ferreteria
    Fuimos a comprar a la ferreteria y como estabamos apurados de tiempo no pedimos factura, ademas era algo accesible asi que lo compramos nosotros.
2024-10-29 feat: agregar fallo
    Quemamos uno de los soportes del motor por utilizar mucho amperaje en la soldadora. Debimos utilizar un electrodo mas pequeño para que no levante tanta temperatura.
2024-10-29 feat: agregar fallo
    La plancha de cobre se inflo por el calor y el toner no se grabo. Creemos que por la suciedad del cobre el toner no se llego a adherir al cobre y posiblemente o quizas estabamos utilizando mucha temp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
2024-10-31 feat: Agregar modelo 3D del acople adaptador de la polea al eje.
    [AgarrePolea.FCStd]
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2024-11-01 fix: Acomordar posición del agujero pasante para que coincida con el de la varilla.
    [AgarrePolea.FCStd]
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2024-11-05 fix: acomodar cantidad de dientes
    [AgarrePolea.FCStd]
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2024-11-05 Feat: corte laser de la prueba de helice (a escala)
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2024-11-06 feat: primera capa de negro de a estructura.
    La segunda capa la haremos a la brevedad luego de instalar los rulemanes para el eje.
2024-11-06 feat: modelos en PAI a escala de la helice
    Luego de 13 pruebas de helice mas, seguimos perfeccionando su recorte para que tenga la forma perfecta.
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2024-11-07 fix: Agregar rellenado de cobre a las zonas por donde no pasan pistas en la pcb.
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2024-11-10 feat: directorio para video, actualización de la ct
2024-11-10 feat: subo antepro, carpeta de campo y reordeno
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2024-11-11 Feat: se probo la pieza en 3D para unir el eje con la polea
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2024-11-16 feat: impresion 3D de los ganchos guia de correa
2024-11-16 feat: corte con amoladora de eje que gira
2024-11-16 feat: termoformado del aspa con pistola de calor
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2024-11-19 fix: cambio en el banner
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2024-11-26 feat: agregar comprobante de pago de la pintura violeta.
2024-11-26 feat: montar diodos al disipador de calor y recortarlo.
2024-11-26 feat: agregar imagen de la primer pala de la helice termoformada.
2024-11-26 feat: caballeta de madera
    Utilizamos este caballete para colocar por encima el recorte del PAI y poder termo formarlo dandole asi forma a las palas.
2024-11-26 feat: recortes en madera para el caballete
    Con estos cortes en madera armamos el caballete para poder termo formar la helice.
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2024-11-28 feat: agregar img polea con topes.
    Polea con los topes impresos en 3D para que la correa no se salga cuando gire a muchas revoluciones.
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
